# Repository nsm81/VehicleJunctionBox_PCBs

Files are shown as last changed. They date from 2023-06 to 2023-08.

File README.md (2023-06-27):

# VehicleJunctionBox
The junction box is an intermediate stage between the accumulator and inverter. It contains an HVD, a current sensor, discharge circuitry, TSAL and TSMPs. 

## PCBs & Enclosure
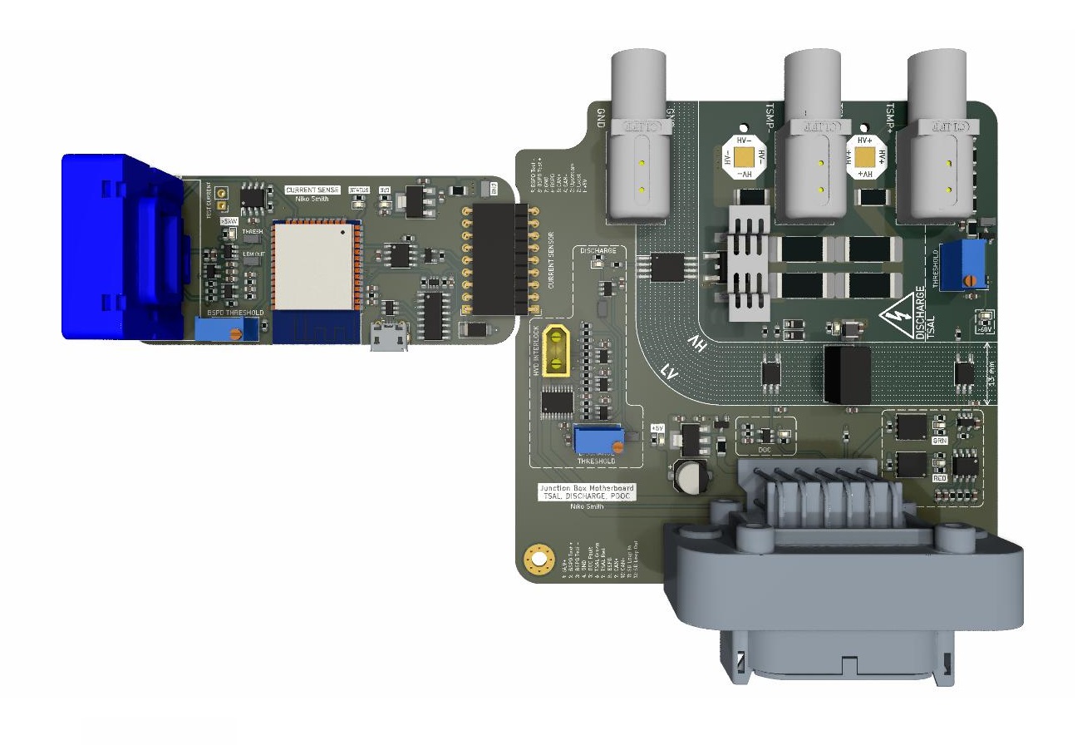
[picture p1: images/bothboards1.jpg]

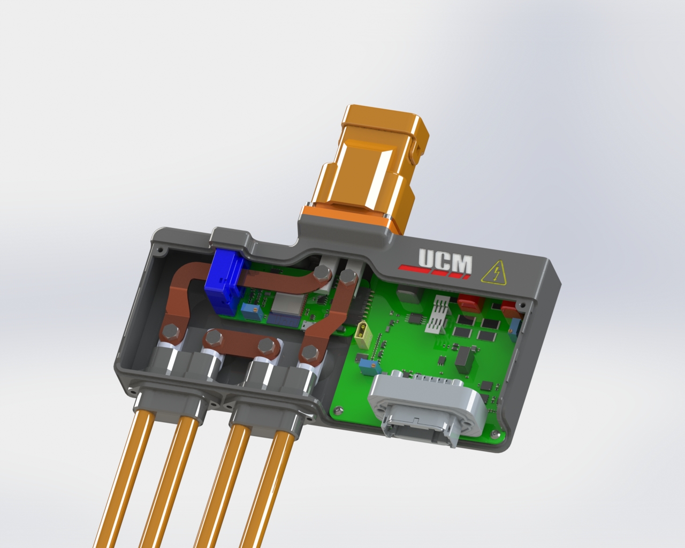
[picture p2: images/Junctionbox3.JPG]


## Block Diagram
Render

## Current Sense MCU IO
| Description  | IO |
| --- | --- |
| Local Fault | IO34 |
| Upstream Fault | IO35 |
| STATUS LED | IO12 |
| CAN RX | IO32 |
| CAN TX | IO26 |
| SDA | IO4 |
| SCL | IO15 |
| VREF | IO19 |
| LEM_OUT | IO21 |

## DTM PinOut
| Pin  | Description |
| --- | --- |
| 1 | GLV+ |
| 2 | BSPD Test Current + |
| 3 | BSPD Test Current - |
| 4 | GND |
| 5 | DOC Fault |
| 6 | TSAL Green |
| 7 | TSAL Red |
| 8 | BSPD 5kW Detect |
| 9 | CAN+ |
| 10 | CAN- |
| 11 | SD Loop In |
| 12 | SD Loop Out |

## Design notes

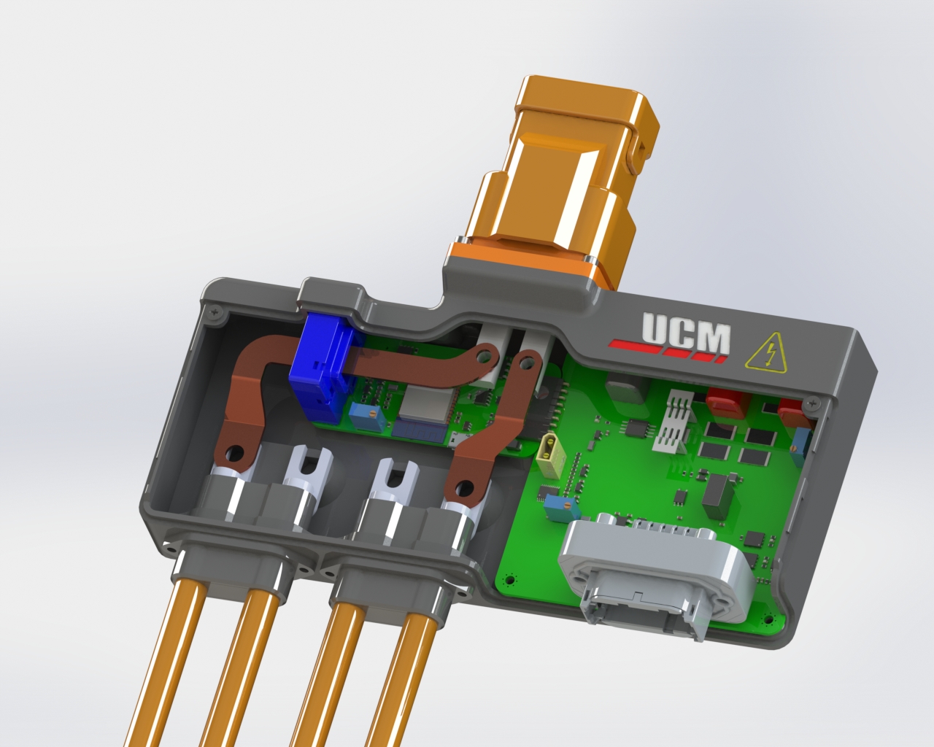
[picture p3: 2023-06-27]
images/Junctionbox2.JPG

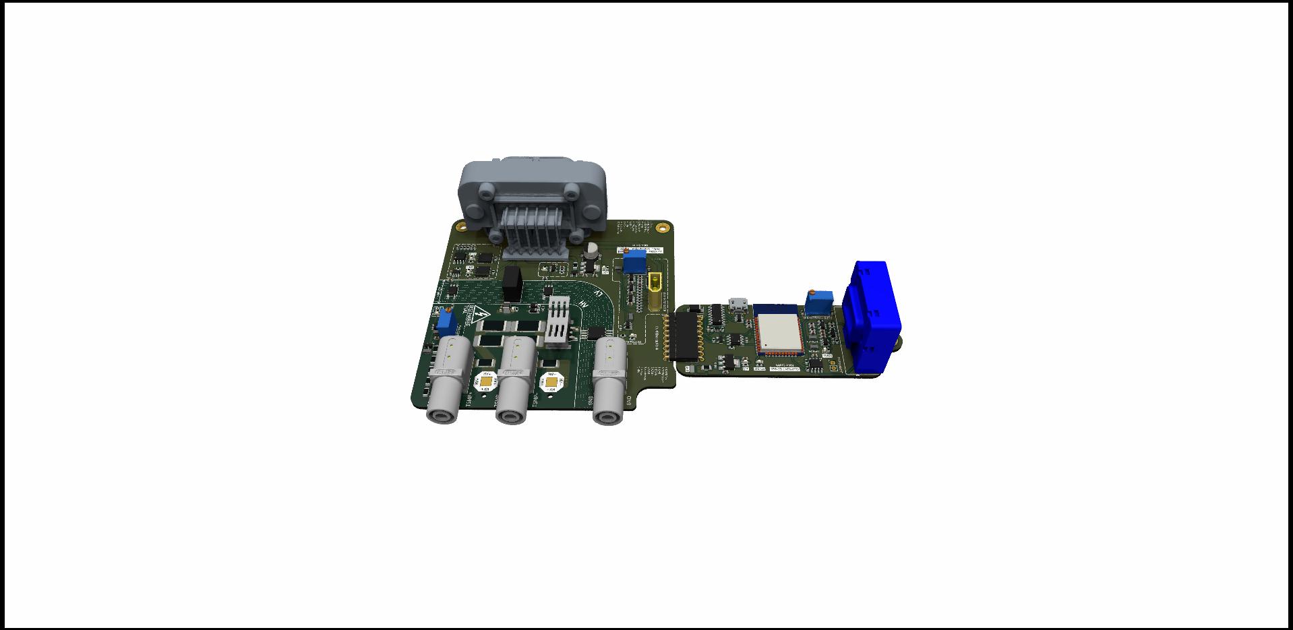
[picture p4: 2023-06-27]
images/bothboards5.jpg

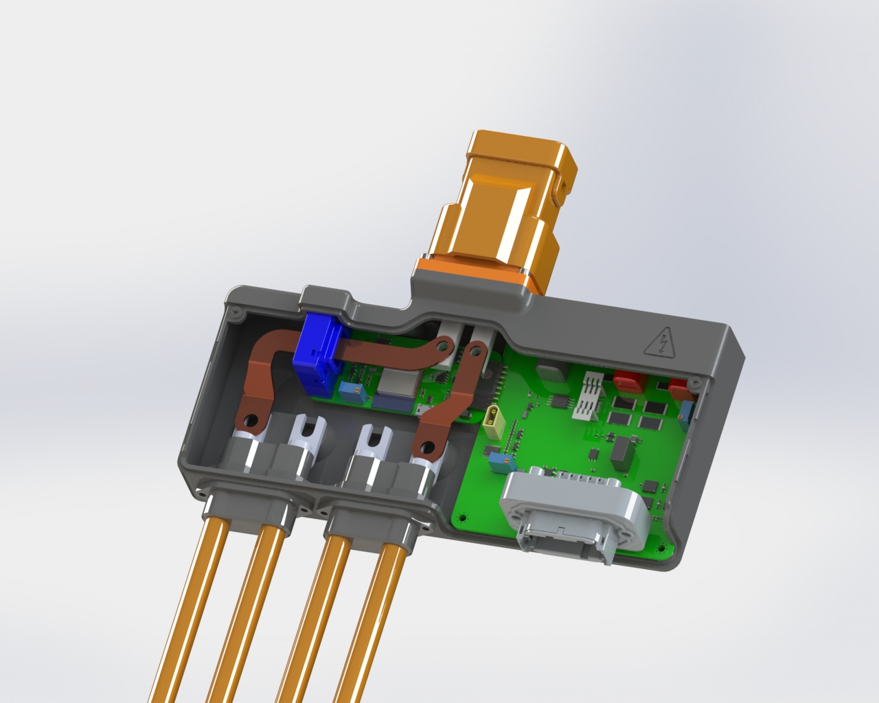
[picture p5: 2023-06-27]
images/Junctionbox1.JPG

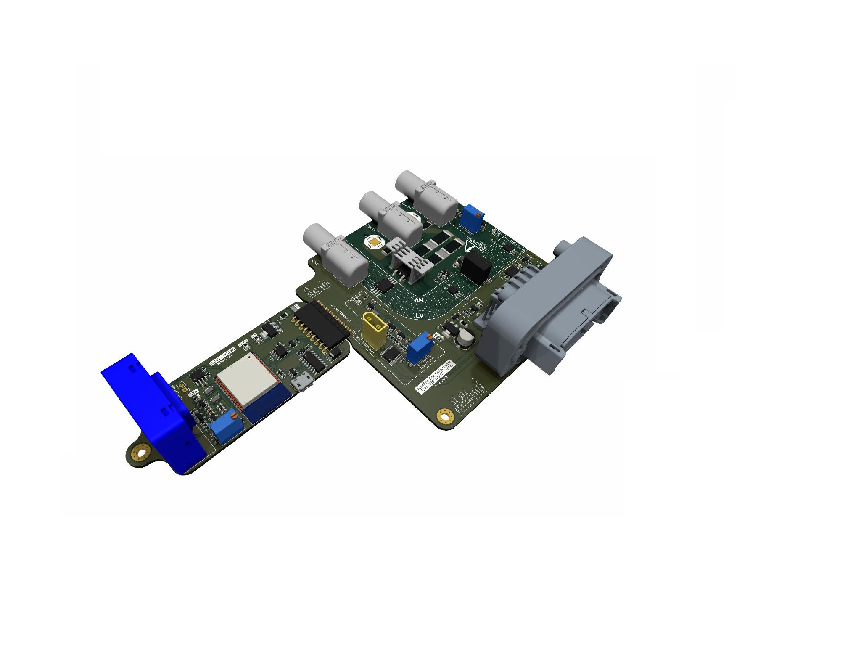
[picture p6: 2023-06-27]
images/bothboards3.jpg

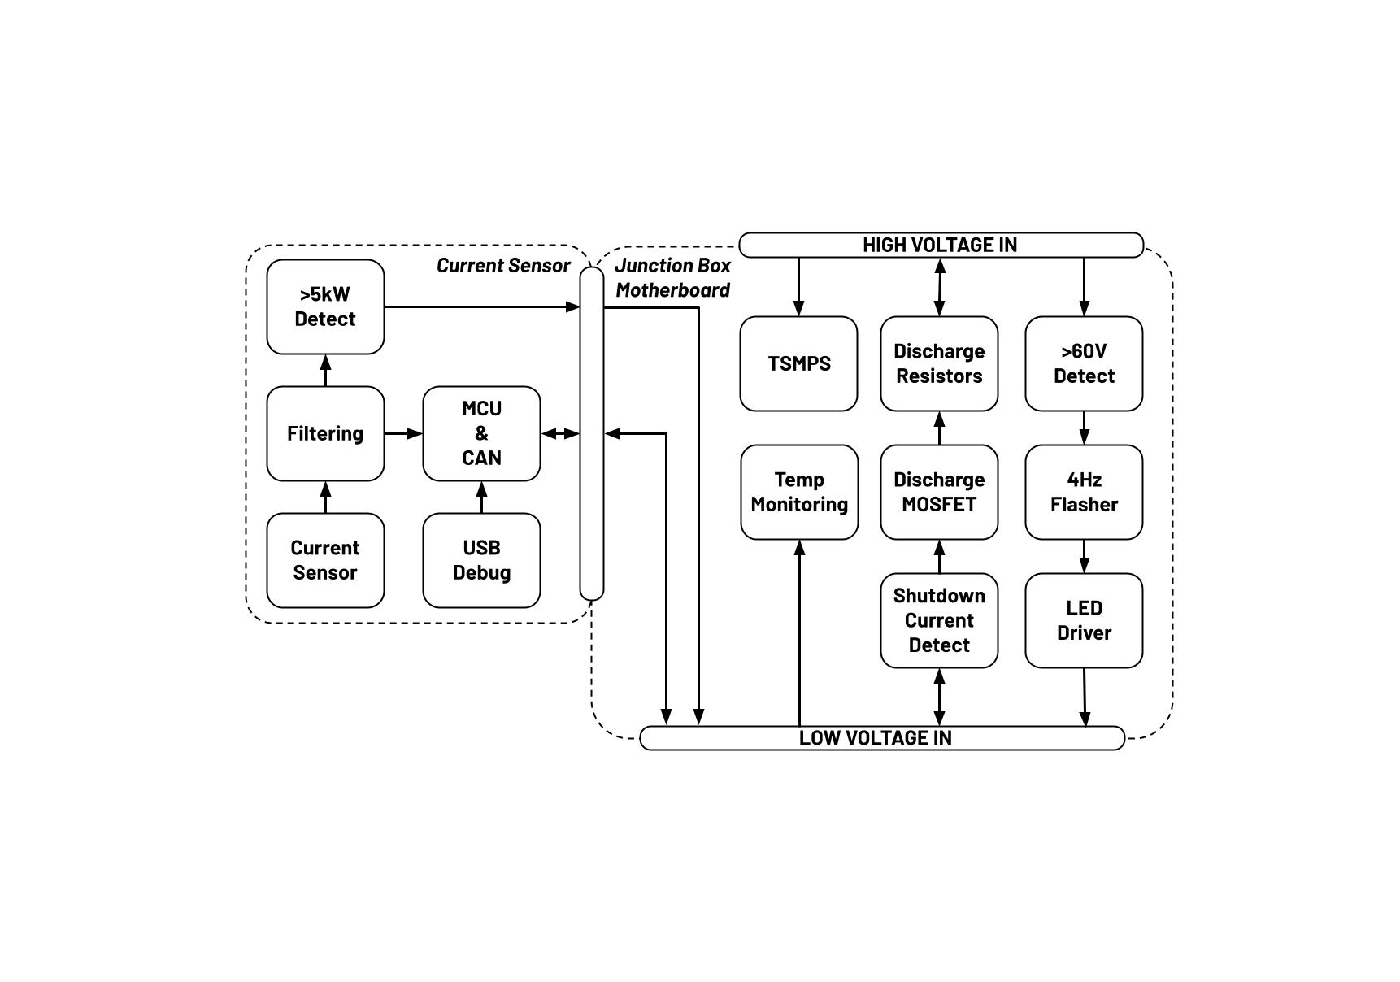
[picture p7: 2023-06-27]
images/VehicleJunctionBoxBlockDiagram.jpg

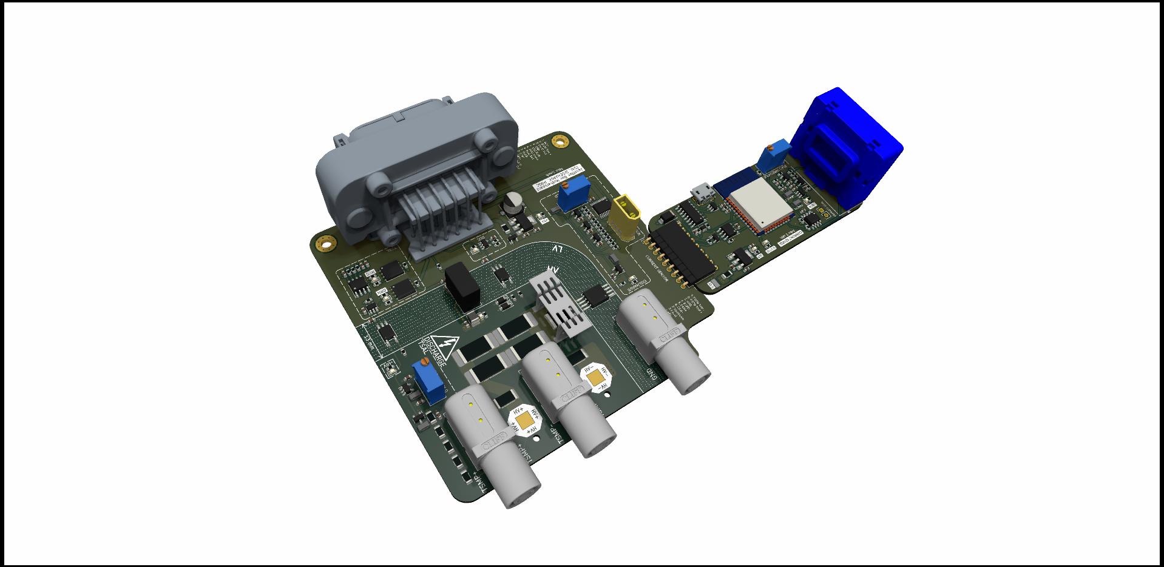
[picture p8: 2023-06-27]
images/bothboards4.jpg

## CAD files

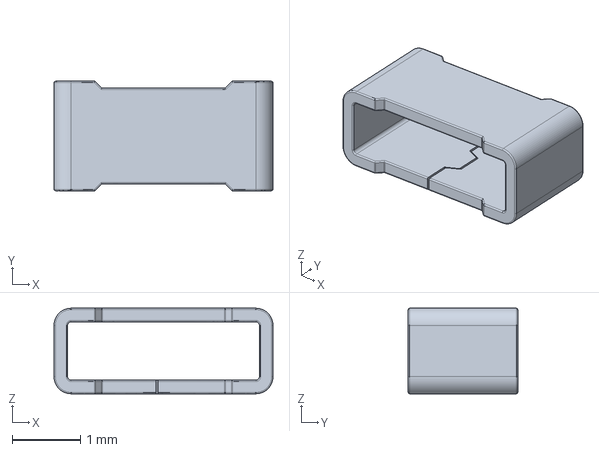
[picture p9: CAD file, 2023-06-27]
VehicleCurrentSense_PCB/3Dmodels/RCS (1206).stp
3.20 x 1.60 x 1.25 mm

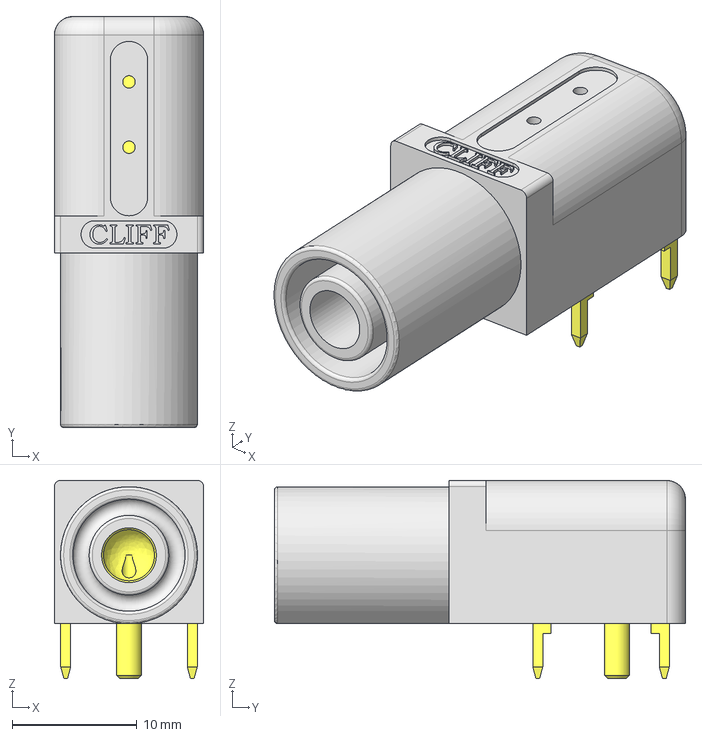
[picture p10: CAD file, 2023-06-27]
VehicleJunctionBoxMotherboard_PCB/3Dmodels/FCR7350.stp
12.0 x 33.0 x 15.9 mm

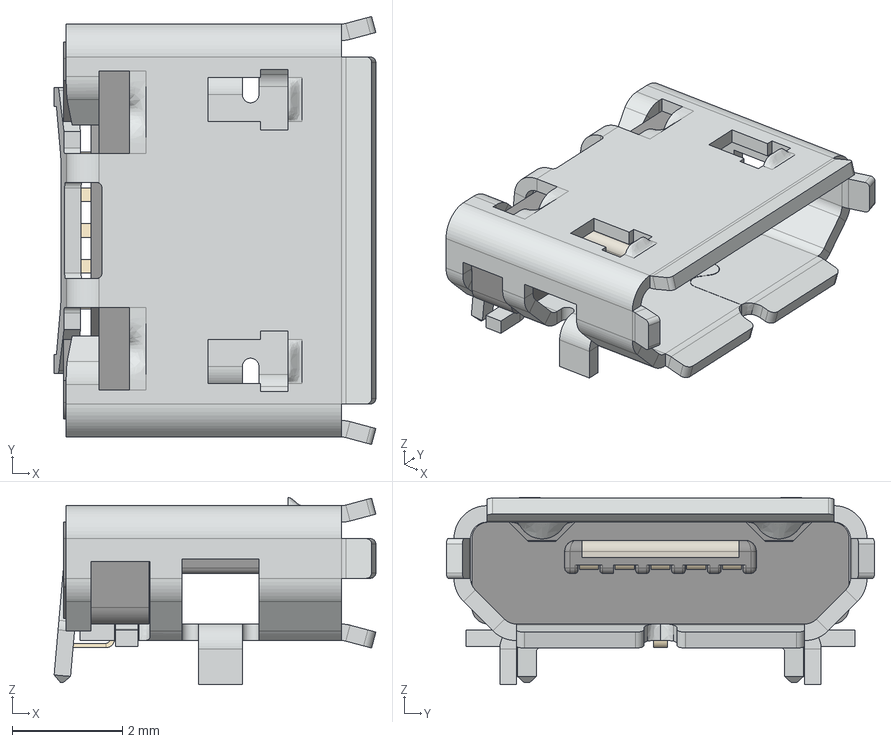
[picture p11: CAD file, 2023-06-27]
VehicleCurrentSense_PCB/3Dmodels/micro_usb_connector.stp
5.84 x 7.77 x 3.40 mm
shield
socket_housing
socket_plate
terminal x 5

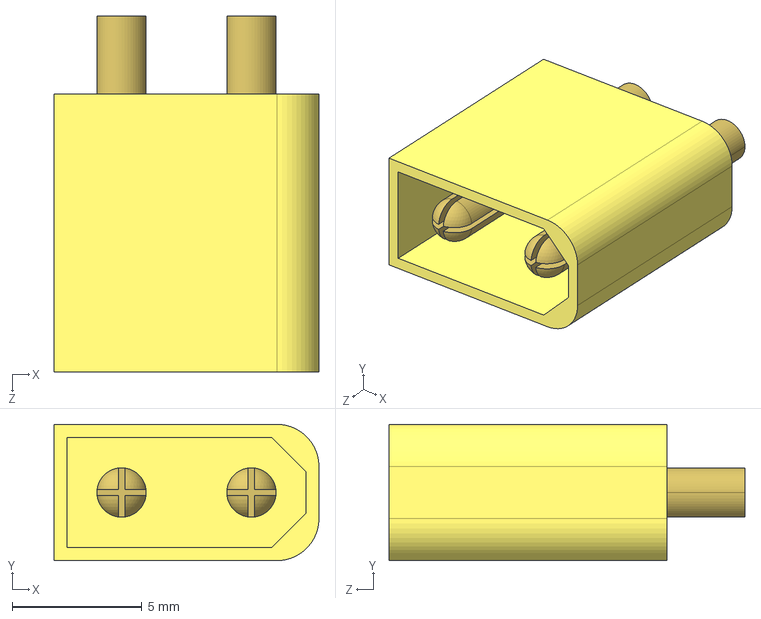
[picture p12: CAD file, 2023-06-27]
VehicleJunctionBoxMotherboard_PCB/3Dmodels/XT30U-M_NEW.STEP
10.2 x 5.25 x 13.7 mm

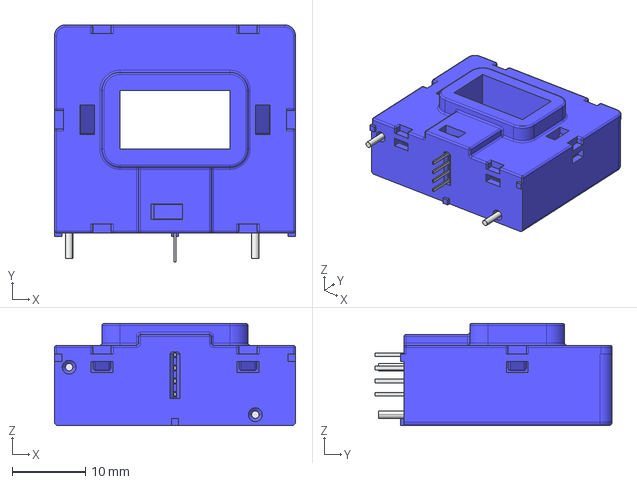
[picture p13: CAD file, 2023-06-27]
VehicleCurrentSense_PCB/3Dmodels/HAIS_3D.stp
33.0 x 32.5 x 14.0 mm

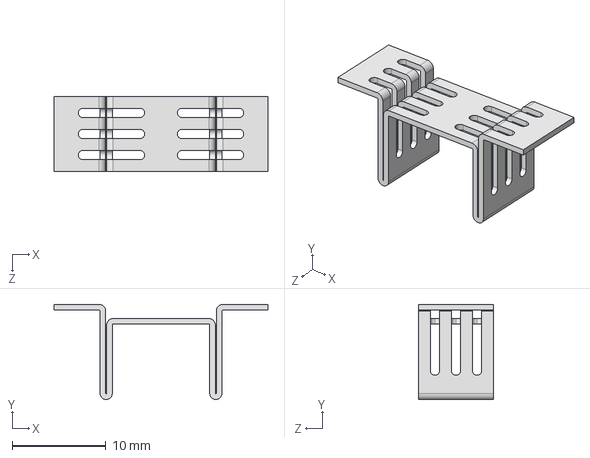
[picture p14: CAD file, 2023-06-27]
VehicleJunctionBoxMotherboard_PCB/3Dmodels/CUI_DEVICES_HSS-C52-NP-SMT-TR.step
22.9 x 10.2 x 8.00 mm

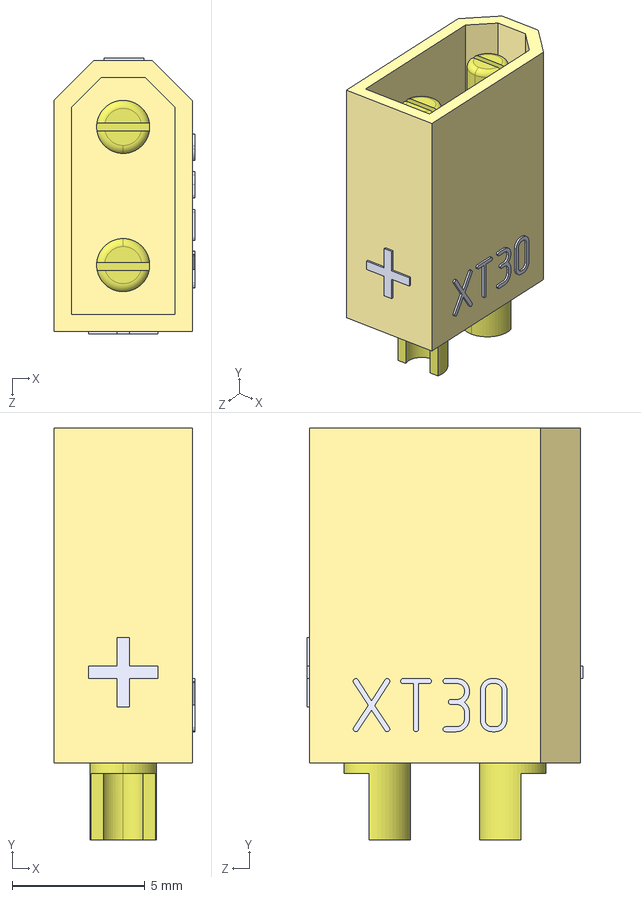
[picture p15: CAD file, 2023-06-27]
VehicleJunctionBoxMotherboard_PCB/3Dmodels/User Library-XT30.step
5.30 x 15.5 x 10.4 mm

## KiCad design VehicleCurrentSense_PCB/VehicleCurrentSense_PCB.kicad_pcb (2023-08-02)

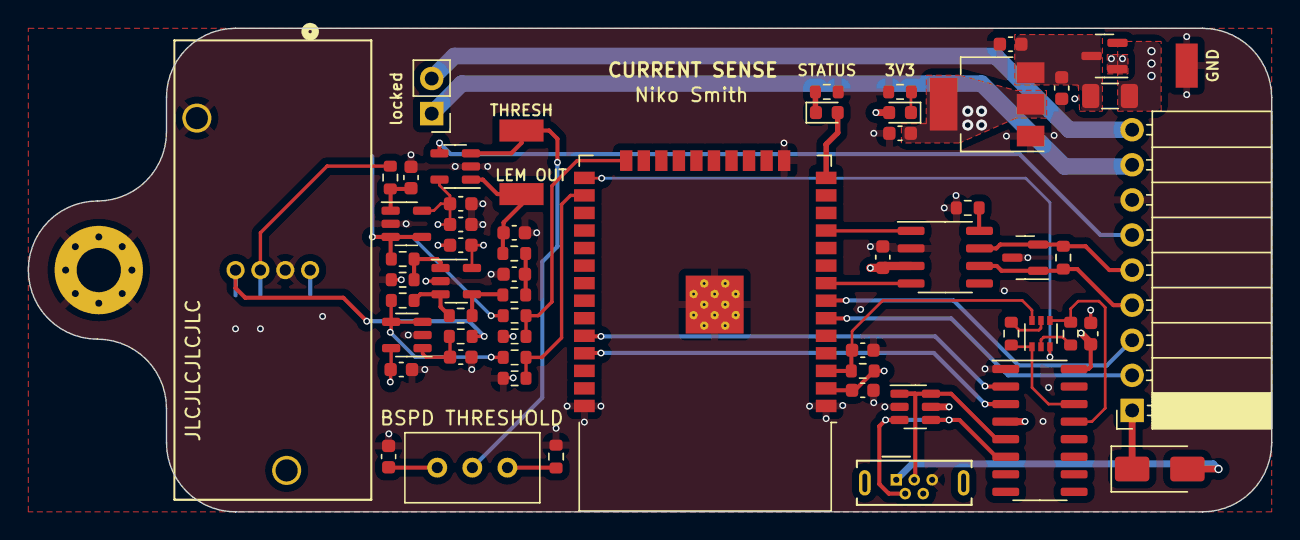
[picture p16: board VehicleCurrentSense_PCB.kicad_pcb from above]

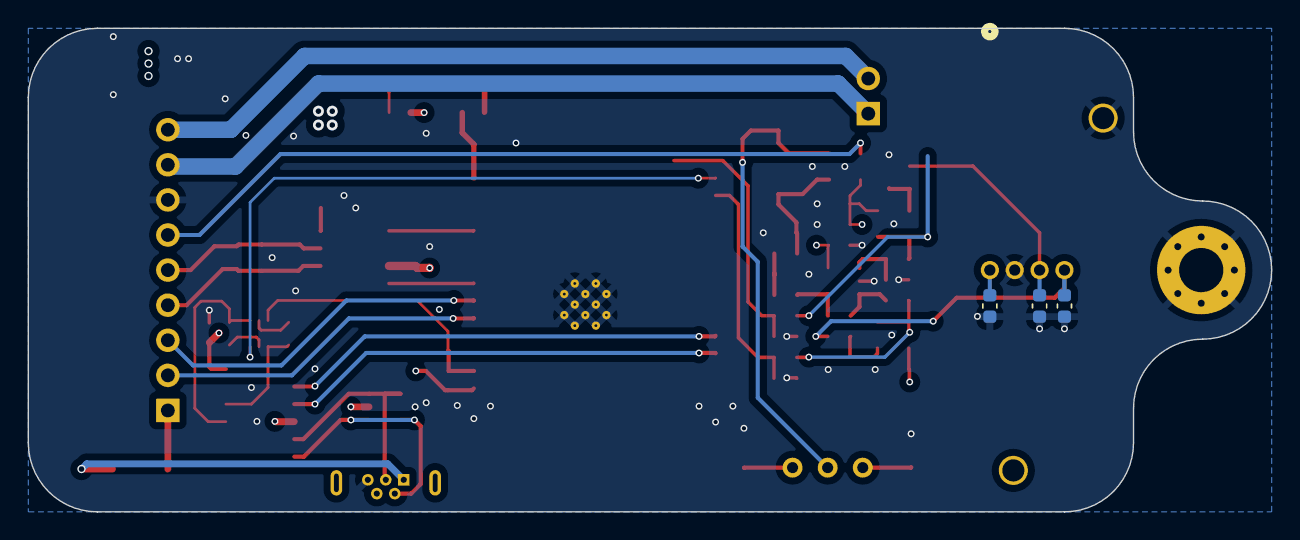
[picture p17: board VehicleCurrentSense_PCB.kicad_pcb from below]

Board: 4 copper layers, 90.0 x 35.0 mm, 64 parts (3 on the bottom side), 43 nets.

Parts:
C1, C3: 47n; C_0603_1608Metric
C2: 4.7n; C_0603_1608Metric
C4, C5: 1u; C_0603_1608Metric
C6, C8, C10, C11, C12, C16, C19, C20: 100n; C_0603_1608Metric
C7, C15: 22u; C_0603_1608Metric
C13: 0.1uF; C_0603_1608Metric
C14, C17, C18: 10u; C_0603_1608Metric
D1: 771-PLVA650A; SOT-23
D2: SS34; D_SMA
D3: GREEN; LED_0603_1608Metric
D4: SM712_SOT23; SOT-23
D5: Green; LED_0603_1608Metric
F1: 1A; Fuse_1206_3216Metric
H2: MountingHole_Pad; MountingHole_3.2mm_M3_Pad_Via
J1: Conn_01x07; PinSocket_1x09_P2.54mm_Horizontal
J3: Test Current; PinHeader_1x02_P2.54mm_Vertical
J4: USB_B_Micro; USB_Micro-B_Wuerth_614105150721_Vertical
Q1: BC847BS; SOT-363_SC-70-6
R1, R2: 3.3k; R_0603_1608Metric
R9: 2.2k; R_0603_1608Metric
R10, R11, R12, R13, R17, R18, R19, R20: 10k; R_0603_1608Metric
R14: 120; R_0603_1608Metric
R21: 4.2k; R_0603_1608Metric
R22, R23: 2k; R_0603_1608Metric
R24, R25, R28: 100k; R_0603_1608Metric
R26, R27: 1.6k; R_0603_1608Metric
RV2: 100k; Potentiometer_Bourns_3296W_Vertical
TP1: GND; 1206 Testpoint
TP3: Vdiff; 1206 Testpoint
TP4: Thresh; 1206 Testpoint
U1: HAIS 100-P; HAIS_P_LEM
U2, U6, U10: LMV321; SOT-23-5
U3: AMS1117-3.3; SOT-223-3_TabPin2
U5: USBLC6-2SC6; SOT-23-6
U7: ESP32-WROOM-32
U8: CH340C; SOIC-16_3.9x9.9mm_P1.27mm
U9: SN65HVD230; SOIC-8_3.9x4.9mm_P1.27mm
U11: TL331; SOT-23-5

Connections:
3V3 LEM_OUT: R17.2, R18.1, U7.24 (IO2)
3V3 VREF: R19.2, R20.1, U7.26 (IO4)
+3V3: C11.2, C12.2, C13.2, C15.1, D5.2 (A), R10.2, U3.2 (VO), U7.2 (VDD), U8.4 (V3), U8.16 (VCC), U9.3 (VCC)
+5V: C3.1, C6.1, C8.1, C16.1, C19.1, C20.1, D2.1 (K), F1.1, J1.1, RV2.3, U1.1 (+5V), U2.5 (V+), U5.5 (VBUS), U6.5 (V+), U10.5 (V+), U11.5 (V+)
BSPD: J1.6, U11.4
BSPD Test Current +: J1.8, J3.1
BSPD Test Current -: J1.9, J3.2
BSPD Threshold: RV2.2, TP4.1, U11.3 (+)
CAN+: D4.2 (A2), J1.5, R14.2, U9.7 (CANH)
CAN-: D4.1 (A1), J1.4, R14.1, U9.6 (CANL)
CAN_RX: U7.8 (IO32), U9.4 (R)
CAN_TX: U7.11 (IO26), U9.1 (D)
D+: J4.3 (D+), U5.1 (I/O1), U5.6 (I/O1), U8.5 (UD+)
D-: J4.2 (D-), U5.3 (I/O2), U5.4 (I/O2), U8.6 (UD-)
DTR: Q1.4 (E2), R12.2, U8.13 (~DTR)
EN: C10.1, Q1.6 (C1), R10.1, U7.3 (EN)
GND: C1.2, C2.2, C3.2, C4.2, C5.2, C6.2, C7.2, C8.2, C10.2, C11.1, C12.1, C13.1, C14.2, C15.2, C16.2, C17.2, C18.2, C19.2, C20.2, D1.1 (A), D4.3 (common), H2.1, J1.7, J4.5 (GND), R9.1, R11.2, R18.2, R20.2, R21.1, R24.2, R28.2, TP1.1, U1.2 (GND), U1.5 (CORE), U2.2 (V-), U3.1 (GND), U5.2 (GND), U6.2 (V-), U7.1 (GND), U7.15 (GND), U7.38 (GND), U7.39 (GND), U8.1 (GND), U9.2 (GND), U10.2 (V-), U11.2 (V-)
IO0: Q1.3 (C2), U7.25 (IO0)
LEM_OUT: R17.1, R23.2, U6.3 (-), U6.4
Local: J1.3, U7.7 (IO35)
unnamed: C17.1, R26.2, R27.1
unnamed: C7.1, C14.1, D1.3 (K), F1.2, U3.3 (VI)
unnamed: D2.2 (A), J4.1 (VBUS)
unnamed: D3.1 (K), R9.2
unnamed: D5.1 (K), R21.2
unnamed: Q1.2 (B1), R12.1
unnamed: Q1.5 (B2), R13.1
unnamed: R25.1, R26.1, U10.4
unnamed: R28.1, RV2.1
unnamed: C2.1, R1.1, U1.3 (OUTPUT)
unnamed: C4.1, R2.2, U2.1 (+)
unnamed: C5.1, R1.2, U6.1 (+)
unnamed: R11.1, U9.8 (Rs)
unnamed: R23.1, R24.1, U10.1 (+)
unnamed: R22.1, R25.2, U10.3 (-)
unnamed: C18.1, R27.2, TP3.1, U11.1 (-)
RTS: Q1.1 (E1), R13.2, U8.14 (~RTS)
RxD: U7.35 (TXD0/IO1), U8.3 (RXD)
Status_LED: D3.2 (A), U7.14 (IO12)
TxD: U7.34 (RXD0/IO3), U8.2 (TXD)
Upstream: J1.2, U7.6 (IO34)
VREF: C1.1, R2.1, U1.4 (VREF)
VREF_OUT: R19.1, R22.2, U2.3 (-), U2.4

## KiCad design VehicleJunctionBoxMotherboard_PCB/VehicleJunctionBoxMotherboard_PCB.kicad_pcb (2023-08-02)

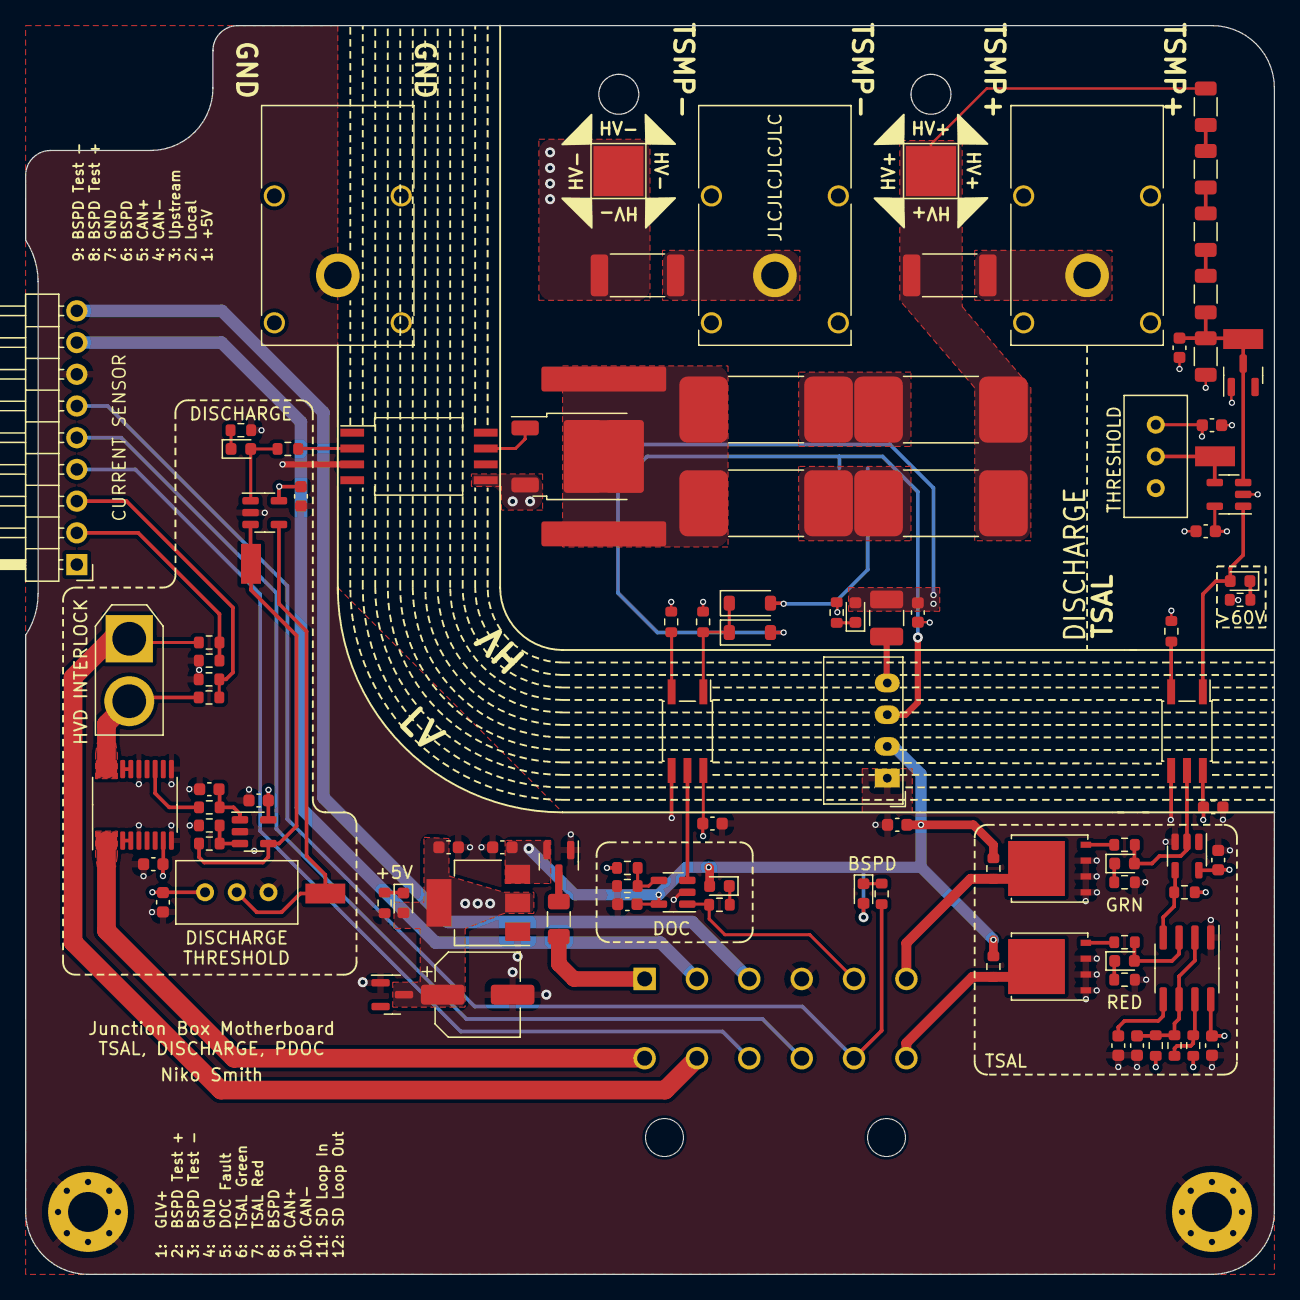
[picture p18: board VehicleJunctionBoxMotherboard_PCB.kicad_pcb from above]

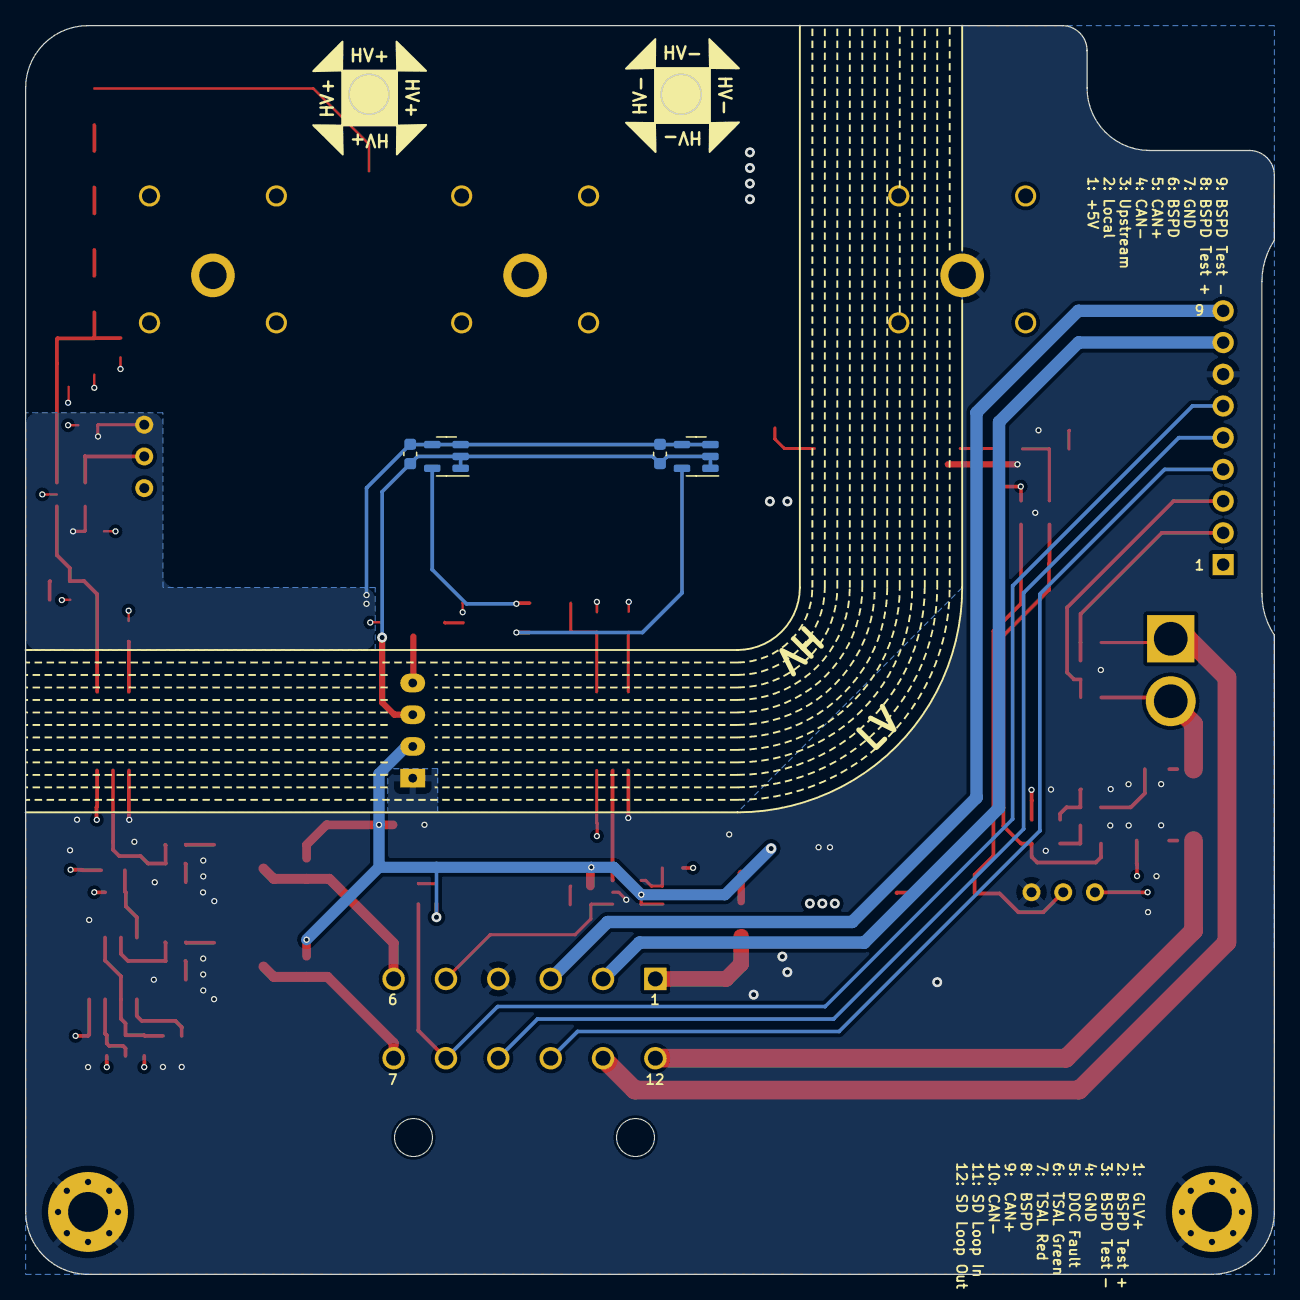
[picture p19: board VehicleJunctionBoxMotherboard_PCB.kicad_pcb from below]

Board: 4 copper layers, 100.0 x 100.0 mm, 111 parts (4 on the bottom side), 66 nets.

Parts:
C1, C2: 22u; C_0603_1608Metric
C3: 330n; C_0603_1608Metric
C4, C5, C6, C10, C11, C12, C13, C14, C16, C18, C19, C20, C23, C25, C26: 100n; C_0603_1608Metric
C7: 4.7u; C_0603_1608Metric
C8: 100u; CP_Elec_6.3x5.4
C15: 10n; C_0603_1608Metric
C17: 10u; C_0603_1608Metric
D1, D2, D4, D5, D6, D7, D12: Green; LED_0603_1608Metric
D3, D11: 771-PLVA650A; SOT-23
D8, D10: 1N4148W; D_SOD-123
D9: Red; LED_0603_1608Metric
F2: 2A; Fuse_1206_3216Metric
H3, H4: MountingHole_Pad; MountingHole_3.2mm_M3_Pad_Via
HS1: Heatsink_Pad_2Pin; MOSFET Heatsink
J1: HVD IL; AMASS_XT30U-F_1x02_P5.0mm_Vertical
J2: Vehicle; TE_DTM13-12PA
J3: TSMP+; Banana_Cliff_FCR7350x_S16N-PC_Horizontal
J4: TSMP-; Banana_Cliff_FCR7350x_S16N-PC_Horizontal
J5: HV+; TestPoint_Pad_4.0x4.0mm
J6: HV-; TestPoint_Pad_4.0x4.0mm
J7: TSMP GLV-; Banana_Cliff_FCR7350x_S16N-PC_Horizontal
J9: Conn_01x07; PinHeader_1x09_P2.54mm_Horizontal
L1: 47u; L_1210_3225Metric_Pad1.42x2.65mm_HandSolder
Q1: IXTY1R6N100D2; TO-252-2
Q3, Q4: FDMS86255; TDSON-8-1
Q5: SSM3J328R LF; SOT-23
R1, R2, R3, R4: DIS-10k; R_4020_10251Metric
R5, R19, R24: 4.7k; R_0603_1608Metric
R6, R9: 15k; R_2512_6332Metric_Pad1.40x3.35mm_HandSolder
R7, R10, R17, R31: 4.2k; R_0603_1608Metric
R8, R11, R20, R23, R33, R49: 10k; R_0603_1608Metric
R12, R13, R14, R15: 510k; R_1206_3216Metric
R16: 25k; R_1206_3216Metric
R18, R30, R35, R37: 1k; R_0603_1608Metric
R21: 1M; R_0603_1608Metric
R22: 16k; R_0603_1608Metric
R25, R26: 100R; R_0603_1608Metric
R27, R28: 100k; R_0603_1608Metric
R29: 11k; R_0603_1608Metric
R32: 330R; R_0603_1608Metric
R39, R43: 5.6k; R_0603_1608Metric
R41, R42: 18k; R_0603_1608Metric
RV1, RV2: 100k; Potentiometer_Bourns_3296W_Vertical
TP1: TS Voltage Divider; 1206 Testpoint
TP2: ISense Out; 1206 Testpoint
TP3, TP4: Thresh; 1206 Testpoint
U1: AMS1117-5.0; SOT-223-3_TabPin2
U2, U6, U10: TLV7031DBV; SOT-23-5
U3, U5: MCP9502PT-115E; SOT-23-5
U4: CRE1S1205SC; Converter_DCDC_Murata_CRE1xxxxxxSC_THT
U7, U20: TLP2361; SO-5_4.4x3.6mm_P1.27mm
U8: SN74LVC1G04DBVT; SOT-23-5
U9: NA555D; SOIC-8_3.9x4.9mm_P1.27mm
U12: INA253; TSSOP-20_4.4x6.5mm_P0.65mm
U13: LMV321; SOT-23-5
U15: ACPL-K30T-000E; SSO-8_6.8x5.9mm_P1.27mm_Clearance8mm

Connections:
+5V: C2.1, C5.2, C8.1, C13.1, C14.1, C16.1, C18.1, C19.1, C20.2, C25.1, D1.2 (A), D11.3 (K), J9.1, R11.1, R20.2, R21.1, R22.1, RV2.3, U1.2 (VO), U7.6 (VDD), U8.5, U9.8 (VCC), U10.5 (V+), U12.9 (VS), U13.5 (V+), U20.6 (VDD)
+5VA: C7.1, C11.1, C12.1, C23.2, C26.2, D2.2 (A), L1.2, RV1.3, U2.5 (V+), U3.3 (Hyst), U3.4 (VDD), U5.3 (Hyst), U5.4 (VDD)
BSPD: J2.8, J9.6, R5.1
BSPD Test Current +: J2.2, J9.8
BSPD Test Current -: J2.3, J9.9
CAN+: J2.9, J9.5
CAN-: J2.10, J9.4
DISCHARGE_THRESHOLD: RV2.2, TP3.1, U10.4 (-)
DOC_FLT: J2.5, R35.1, U6.1
DOC_Thresh: R11.2, R33.1, U6.4 (-)
GLV+: C1.1, C4.2, C6.1, D6.2 (A), D12.2 (A), Q5.2 (S), R27.1, R28.1, U1.3 (VI), U4.2 (+VIN), U6.5 (V+)
GND: C1.2, C2.2, C3.2, C4.1, C5.1, C6.2, C8.2, C13.2, C14.2, C15.2, C16.2, C17.2, C18.2, C19.2, C20.1, C25.2, D11.1 (A), H3.1, H4.1, J2.4, J7.1, J9.7, Q3.1 (S), Q3.2 (S), Q3.3 (S), Q4.1 (S), Q4.2 (S), Q4.3 (S), Q5.1 (G), R7.1, R19.2, R24.2, R30.1, R31.1, R33.2, R39.2, R43.2, RV2.1, U1.1 (GND), U4.1 (-VIN), U6.2 (V-), U7.4 (GND), U8.3, U9.1 (GND), U10.2 (V-), U12.6 (GND), U12.10 (REF2), U12.11 (REF1), U12.15 (GND), U13.2 (V-), U15.3, U20.4 (GND)
HV+: J5.1, R3.2, R4.2, R6.1, R12.2
HV-: C7.2, C10.2, C11.2, C12.2, C23.1, C26.1, D3.1 (A), J6.1, Q1.3 (S), R9.1, R10.1, R16.1, R17.1, R18.1, R37.1, R49.1, RV1.1, U2.2 (V-), U3.1 (GND), U3.2 (GND), U4.3 (-VOUT), U5.1 (GND), U5.2 (GND), U15.5
Local: J9.3, R41.2, R43.1
unnamed: D1.1 (K), R7.2
unnamed: D2.1 (K), R10.2
unnamed: C10.1, D3.3 (K), R15.1, R16.2, TP1.1, U2.3 (+)
unnamed: D4.2 (A), U2.1, U7.1 (A)
unnamed: D4.1 (K), R17.2
unnamed: D5.2 (A), R32.2, U10.1
unnamed: D5.1 (K), R31.2
unnamed: D6.1 (K), R35.2
unnamed: D7.2 (A), R25.1, U7.5 (VO), U8.2
unnamed: D7.1 (K), R19.1
unnamed: D8.2 (A), U5.5 (Out)
unnamed: D9.2 (A), R26.1, U9.3 (Q)
unnamed: D9.1 (K), R24.1
unnamed: D10.2 (A), U3.5 (Out)
unnamed: D8.1 (K), D10.1 (K), R49.2, U20.1 (A)
unnamed: D12.1 (K), R5.2
unnamed: F2.1, J2.1
unnamed: J3.1, R6.2
unnamed: J4.1, R9.2
unnamed: HS1.1, HS1.2, Q1.2 (D), R1.1, R2.1
unnamed: Q1.1 (G), U15.7
unnamed: Q3.4 (G), R25.2
unnamed: Q4.4 (G), R26.2
unnamed: F2.2, Q5.3 (D)
unnamed: R1.2, R3.1
unnamed: R2.2, R4.1
unnamed: R12.1, R13.2
unnamed: R13.1, R14.2
unnamed: R14.1, R15.2
unnamed: R32.1, U15.2
unnamed: L1.1, U4.4 (+VOUT)
unnamed: R18.2, U7.3 (K)
unnamed: C15.1, U9.5 (CV)
unnamed: R22.2, R23.1, U9.7 (DIS)
unnamed: C17.1, R21.2, R23.2, U9.2 (TR), U9.6 (THR)
unnamed: R29.1, TP2.1, U10.3 (+), U13.4
unnamed: U12.16 (IN+), U12.17 (SH+)
unnamed: U12.4 (SH-), U12.5 (IN-)
unnamed: R8.1, U12.13 (OUT)
unnamed: C3.1, R8.2, U13.1 (+)
unnamed: R29.2, R30.2, U13.3 (-)
unnamed: R37.2, U20.3 (K)
unnamed: U6.3 (+), U20.5 (VO)
RESET: R20.1, U8.4, U9.4 (R)
SD_LP_FROM_HVD: J1.2, R41.1, U12.18 (IS+), U12.19 (IS+), U12.20 (IS+)
SD_LP_IN: J1.1, J2.11, R42.1
SD_LP_OUT: J2.12, U12.1 (IS-), U12.2 (IS-), U12.3 (IS-)
TS Detection Threshold: RV1.2, TP4.1, U2.4 (-)
TSAL_GRN: J2.6, Q3.5 (D), R27.2
TSAL_RED: J2.7, Q4.5 (D), R28.2
Upstream: J9.2, R39.1, R42.2
